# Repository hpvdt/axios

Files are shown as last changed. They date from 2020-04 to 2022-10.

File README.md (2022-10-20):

*This is the repository for our human powered submarine Axios, that we have decided to no longer to pursue. **IT IS NOT COMPLETE, LET ALONE TESTED.***

*Our motivation for making this repository public to to share what progress we did make to help others who might be interested in developing a similar system.*

# Axios

Our attempt at a human powered submarine, titled Axios. Within it there were two electronics systems to be implemented: rebreather monitoring and navigation. These were meant to be operate entirely independently of one another, being powered off separate batteries.

In this repository resides the code and hardware design files prepared for the initial versions of these systems from before the team decided to cancel the project.

Both systems were based around ATmega328P microcontrollers due to the team's familiarity with them and their adaquate amount of peripherals for serving both roles.

## Rebreather System

This was meant to supervise the different gas sensors around the submarine hull to inform the pilot about the atmospheric state within Axios. It collected data from three oxygen sensors and one carbon dioxide (CO2) sensor, it then displayed the value of each on separate seven-segment displays.

Of the two systems prepared for Axios, this was by far the more mature one. It was essentially ready for final deployment.

### Carbon Dioxide Sensing

For monitoring CO2 an MH-Z19 sensor was used which uses infrared to measure CO2 in the air. Getting data with the sensor was simple, it outputs a PWM signal at 1Hz that was trivial to monitor using the ATmega328P. The only hardware needed to interface it with the Arduino was a level shifting transistor to step the 3.3V PWM signal to 5V for the microcontroller to read.

One minor note we were unaware of is that the sensor has a small heater within it which is used to measure the CO2. This means the sensor occasionally draws a surge of current to keep it warm. This caused us to think the system was malfunctioning and drawing excessive power in our preliminary tests.

### Oxygen Sensing

This was the main focus of this board, since we were responsible for reading the raw sensor data. The oxygen sensors we were planning to use were standard oxygen sensors used for SCUBA diving. These are essentially chemical cells that when exposed to varying concentrations of oxygen in the air would vary their voltage proportionally. They had two issues the circuit needed to address:

1. The output voltage was pretty small. About 65mV for a new cell at 100% oxygen, but we would ideally be monitoring 21%, so about 20mV.
2. Although roughly linear, the output at 0% was not 0 mV, but about 15 mV.
3. Being chemical cells, they would gradually degrade and our circuit would need to be tuned for this.

The solution for this was a set of of high precision amplifiers made from operational amplifiers. These would buffer and then amplifier the sensor output to a level more easily read by the ATmega with its internal ADC resolution of about 4 mV. To adjust the circuit for the sensors as they aged we would conduct a two-point calibration (at 100% and 21% oxygen levels) adjusting potentiometers to get the display values to match these conditions.

## Navigation

Axios was designed to be controlled by three servo-actuated control fins. These needed a microcontroller to receive input from the captain (?) and actuate them accordingly. In addition to steering the submarine, it was planned for the captain of Axios to be provided orientation data about the submarine (roll, pitch, yaw), depth information, and power from their pedals. 

This board needs significant revision before it is worthy of installation into any submarine.

### Steering

Steering was to be done using a modified game controller (so we had wires directly to the potentiometers within it) which was read as an analog signal and then following some linear algebra, servo angles would be determined and set. Intentionally a short and simple loop.

There was discussion of a feature to have the submarine maintain depth without user input, but we never reached this stage.

### Orientation Data

Orientation data was meant to be provided by the use of a 9-axis IMU attached to the board. This approach quickly revealed a few key issues:

- The boards were going to move frequently within Axios, and the IMU would need to be calibrated for each new position. This could be remedied by off-boarding the IMU to a set location in Axios.
- The IMU only provided accelerations and magnetic field, we would need to code or find a library to perform the sensor fusion on the ATmega.
   - This would likely lead to significant usage of processor time
   - Our solution may not be able to replicate a more polished sensor even after significant work

Little was done for this as we were planning to transition to another IMU, the BNO055 which would address both of these points.

### Depth Information

Reading the depth was done using a pressure sensor that was connected to a port in the hull. The one we had acquired for Axios output a simple linear output proportional to the pressure sensed and a slight constant offset. Reading this analog signal, then dividing by the specific gravity of water would allow us to accurately estimate our depth in water.

### Pedal Power Data

This was planned to use a Raspberry Pi Zero with an ANT dongle to read available ANT data from the commercial power pedals in Axios and then broadcast it over UART to the microcontroller to display it for the rider.

This never really reached development, although it would likely be heavily based off the working ANT code prepared for [TITAN (2019)](https://github.com/hpvdt/titan_2019).

## Displays

The display system was identical across the boards. Given the amount of pins that needed to be controlled for all the displays a shift register was used for each display to control the segments as the digits were multiplexed by the microcontroller. This meant that all displays on a board could be controller by a handful of pins on the ATmega and a series of daisy-chained shift registers.

Although the two boards would operate separately, they were designed to be roughly arranged as shown below. These displays were meant to be bright enough to pass through the back of the partial mirror used to provide the captain a view.

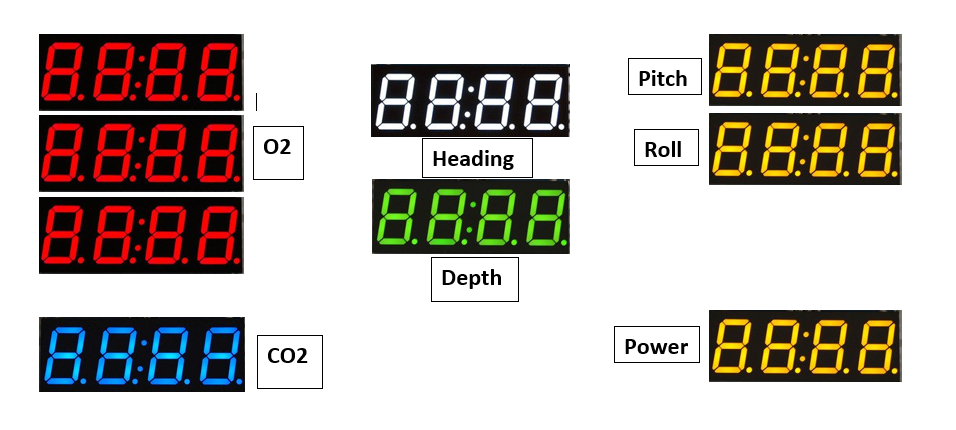
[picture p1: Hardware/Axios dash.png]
Planned Axios layout


# Software Used

For the design of the hardware EAGLE was used. For the microcontroller code it was all prepared using the Arduino IDE.

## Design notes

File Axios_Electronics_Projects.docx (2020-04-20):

# Axios Electronics Projects

Axios is a unique project in many respects, presenting unique challenges and conditions for the electronics to perform in. Reliability and safety are of the utmost importance, and that there is always a ‘fail-safe’ state. All projects are critical unless otherwise noted. All systems need to be splash resistant to a minimum as well.

As with Titan (and probably most of our project going forward,) this system will be powered off several LiFePO4 batteries given their proven stability and safety even when failing.

# Control System

There 3 fins positioned around midway on the sub, spaced 120 degrees apart (front view of the sub to the right). These are positioned using linkages to servos. We need to control these servos based on input from the rider, ideally, they use a single joystick to control pitch, roll, and yaw. This system should be isolated from any other system (excluding navigation).

Tasks for this are:

- Writing code for determining fin angles based on a desired rotation rate
- Getting or making a 3-axis flight stick
  - Must be compact enough to fit in the sub
- Writing code to translate the desired fin angles to servo angles

Skills needed/learned:

- C++ coding
- Basic circuitry
- Potential for circuit board design

# Navigation system

To assist the rider in navigation especially in this unconventional configuration let alone environment, there is a need for navigational sensors. These need to display their data in an easy to read and see location, likely using 7-segment displays for numeric values. This is to me developed alongside the control system and likely share hardware if possible. The data required for the rider are:

- Compass heading, using compass sensor – probably as part of a 9DoF module
- Pitch, using an accelerometer – probably as part of a 9DoF module
- Depth, determined using a special depth sensor

Tasks for this are:

- Writing code for collecting this data
- Writing code for / designing the display circuits

Skills needed/learned:

- C++ coding
- Basic circuitry
- Potential for circuit board design

# Oxygen Sensor System

Absolutely critical! This must be an entirely isolated system of its own. Using three oxygen sensors around the hull, it will display the partial pressure of oxygen in the submarine at each point using 7-segment displays. The values will be to three significant figures between 0 and 1, e.g. 0.201 but it will just display ‘201’.

These sensors output analog signals that will require amplification to be processed by our microcontroller which will require the use of operation amplifiers. The 7-segment display also needs to be prepared but will likely be okay if it is a copy of the ones used for the navigational system.

Skills needed/learned:

- Advanced circuit design
- Micro controller (C/C++) implementation and coding
- Breadboard prototyping
- Circuit board design

# Circuit board design

Pretty self explanatory, design the circuits to connect all the hardware in the sub. Note, there will likely be several different boards present in the sub:

- Control
- Oxygen Sensor
- 7-segment display arrays

Skills needed/learned:

- Circuit design
- Using PCB design software
- Circuit assembly
- Circuit debugging

# Pump System

We need a pump to remove water from our leaks during a ride. This will be a basic system that should only consist of a battery, switch, and pump. All connections should be adequately protected from water.

Pump (has to be high pressure to eject water from the submarine): https://www.banggood.com/FL-3308-130PSI-6LMin-Water-High-Pressure-Diaphragm-Pump-Caravan-Boat-DC12V-p-1071746.html?ID=514178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

Battery: https://hobbyking.com/en_us/zippy-compact-4200mah-4s2p-30c-lifepo4-pack.html?___store=en_us

Skills needed/learned:

- BASIC circuitry
- Basic circuit assembly

# Lights – Optional

In some instances, the sub may need to traverse though darker environments which may need some extra lighting. This is not in the near future however.

Skills needed/learned:

- Circuit design

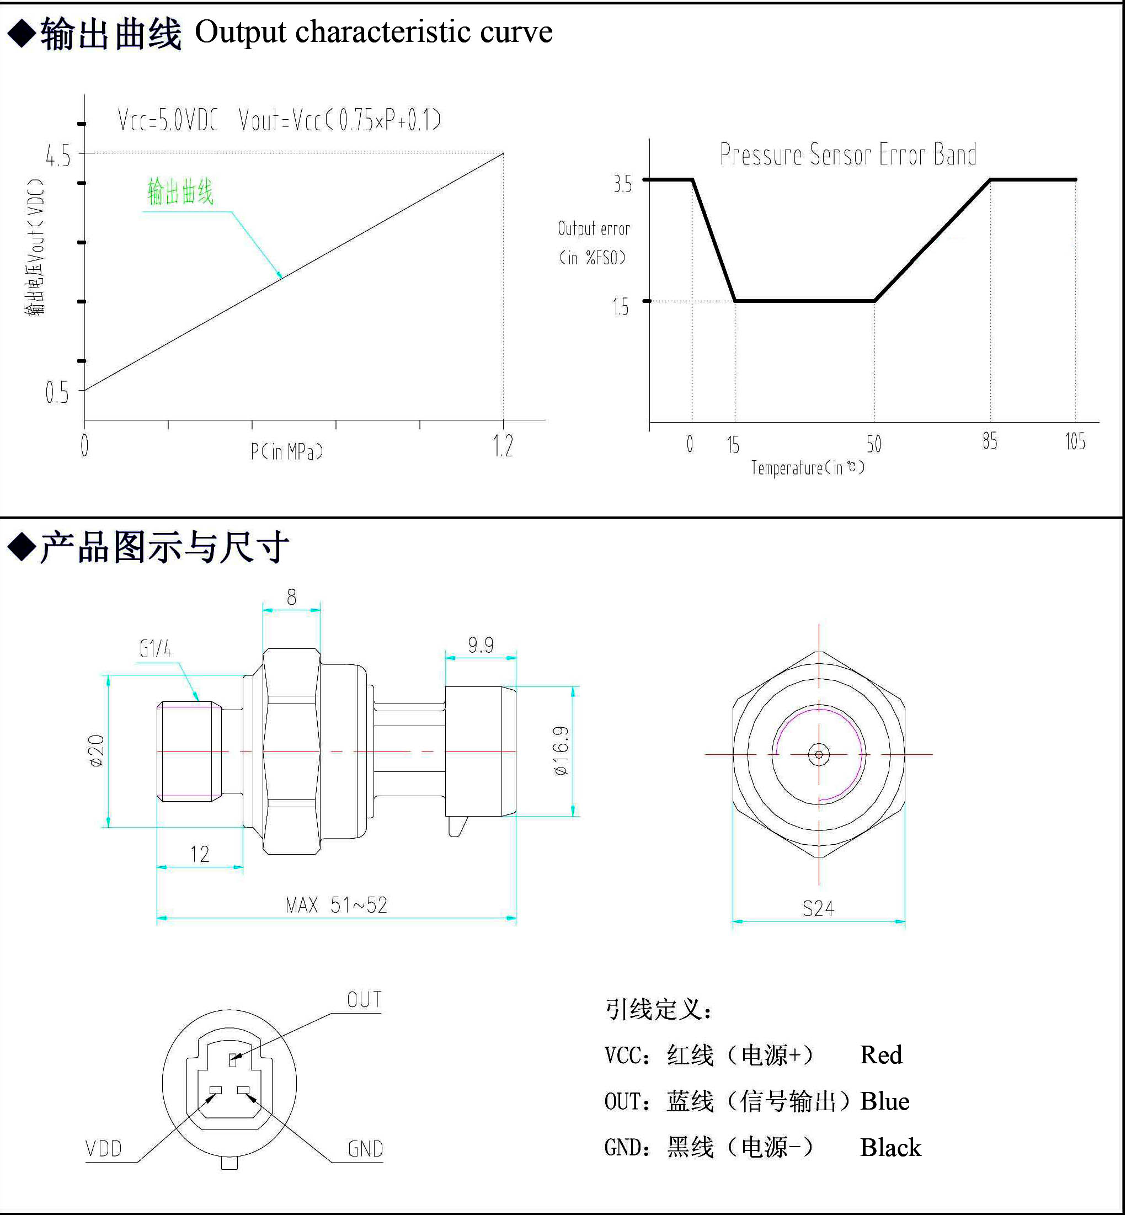
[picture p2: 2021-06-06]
Hardware/control_system/Pressure Sensor Data Sheet.jpg

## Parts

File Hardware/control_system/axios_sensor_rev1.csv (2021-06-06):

Qty | Value | Package | Parts
1 |  | 1X2MTA | J1
7 | 0.1u | C0603 | C2 C4 C6 C8 C10 C12 C18
1 | 0.82u | ECS-MPIL0630-R82MC | L2
1 | 1.5n | C0603 | C5
2 | 1.5u | C0603 | C16 C17
5 | 100k | R0603 | R16 R17 R18 R19 R22
1 | 100u | C0603 | C1
9 | 10k | R0603 | R1 R6 R8 R9 R10 R12 R14 R15 R21
1 | 10n | C0603 | C7
1 | 12k | R0603 | R13
2 | 15k | R0603 | R7 R20
4 | 1k | R0603 | R2 R3 R4 R5
1 | 1u | C0603 | C11
4 | 22u | C0603 | C9 C13 C14 C15
1 | 33u | SRN1060-330M | L1
1 | 47u | C0603 | C3
1 | 52k | R0603 | R11
5 | 7SEGMINI | 7SEGMINI | LED_DEPTH LED_HEADING LED_PITCH LED_POWER LED_ROLL
1 | ACT4065ASH-T | SO8 | U2
1 | AP62600SJ-7 | V-QFN2030-12 | U3
1 | ATMEGA328P_TQFP | TQFP32-08 | U1
5 | CAY16-681J8LF | CAY16-681J8LF | RN1 RN2 RN3 RN4 RN5
1 | CSTNE16M0V530000R0 | CSTCR6M | U$1
1 | CTRL_CONNECT | 1X06 | JP6
1 | Depth Sensor | 1X03 | JP1
1 | ISP | 2X03 | JP7
1 | MPU9250 | MPU9250 | M2
1 | NCP164CSN330T1G | TSOP-5 | U4
1 | SER_CONNECT | 1X06 | JP5
5 | SN74HCS595QPWRQ1 | TSSOP16 | IC2 IC4 IC6 IC8 IC10
1 | Servo1 | 1X03 | JP2
1 | Servo2 | 1X03 | JP3
1 | Servo3 | 1X03 | JP4
1 | V4PAN50-M3 | SMPA | D2
4 | XP231P0201TR | SOT23 | Q1 Q2 Q3 Q4

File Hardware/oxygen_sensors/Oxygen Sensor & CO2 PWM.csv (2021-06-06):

Qty | Value | Device | Package | Parts | Description
3 |  | PINHD-1X2 | 1X02 | SENSOR_1 SENSOR_2 SENSOR_3 | PIN HEADER
32 |  | R-US_R0603 | R0603 | R20 R21 R22 R23 R24 R25 R26 R27 R29 R30 R31 R32 R33 R34 R35 R36 R38 R39 R40 R41 R42 R43 R44 R45 R47 R48 R49 R50 R51 R52 R53 R54 | RESISTOR American symbol
3 | 0.7k | R-US_R0603 | R0603 | R2 R4 R6 | RESISTOR American symbol
7 | 100k | R-US_R0603 | R0603 | R1 R3 R5 R28 R37 R46 R55 | RESISTOR American symbol
2 | 10k | R-US_R0603 | R0603 | R10 R14 | RESISTOR American symbol
6 | 10k | TRIM_US-RJ9W | RJ9W | CAL1 CAL2 CAL3 GAIN_1 GAIN_2 GAIN_3 | POTENTIOMETER
4 | 10n | C-USC0603 | C0603 | C2 C3 C4 C5 | CAPACITOR American symbol
1 | 16MHz | CSTNE16M0V530000R0 | CSTCR6M | Y1
2 | 1u | C-USC0603 | C0603 | C1 C6 | CAPACITOR American symbol
1 | 5V | LD117ASTR | SOT223 | IC3 | Low drop fixed and adjustable positive voltage regulators 1 A
4 | 7SEGMINI | 7SEGMINI | 7SEGMINI | LED2 LED3 LED4 LED5
2 | AD712R | AD712R | SO8 | IC1 IC2 | Dual Precision Low Cost High Speed BiFET Op Amp
1 | ATMEGA328P_TQFP | ATMEGA328P_TQFP | TQFP32-08 | U1 | Popular 328P in QFP
1 | BATT | PINHD-1X2 | 1X02 | BATT | PIN HEADER
1 | CO2 | PINHD-1X3 | 1X03 | CO2 | PIN HEADER
1 | ISP | PINHD-2X3 | 2X03 | ISP | PIN HEADER
1 | SER | PINHD-1X6 | 1X06 | SER | PIN HEADER
4 | SN74HCS595QPWRQ1 | SN74HCS595QPWRQ1 | TSSOP16 | IC4 IC5 IC6 IC7
1 | SST5485 | SST5485 | SOT23 | Q1 | N-Channel JFETs
4 | XP231P0201TR | XP231P0201TR | SOT23 | Q2 Q3 Q4 Q5 | P-Channel Enhancement mode MOSFET

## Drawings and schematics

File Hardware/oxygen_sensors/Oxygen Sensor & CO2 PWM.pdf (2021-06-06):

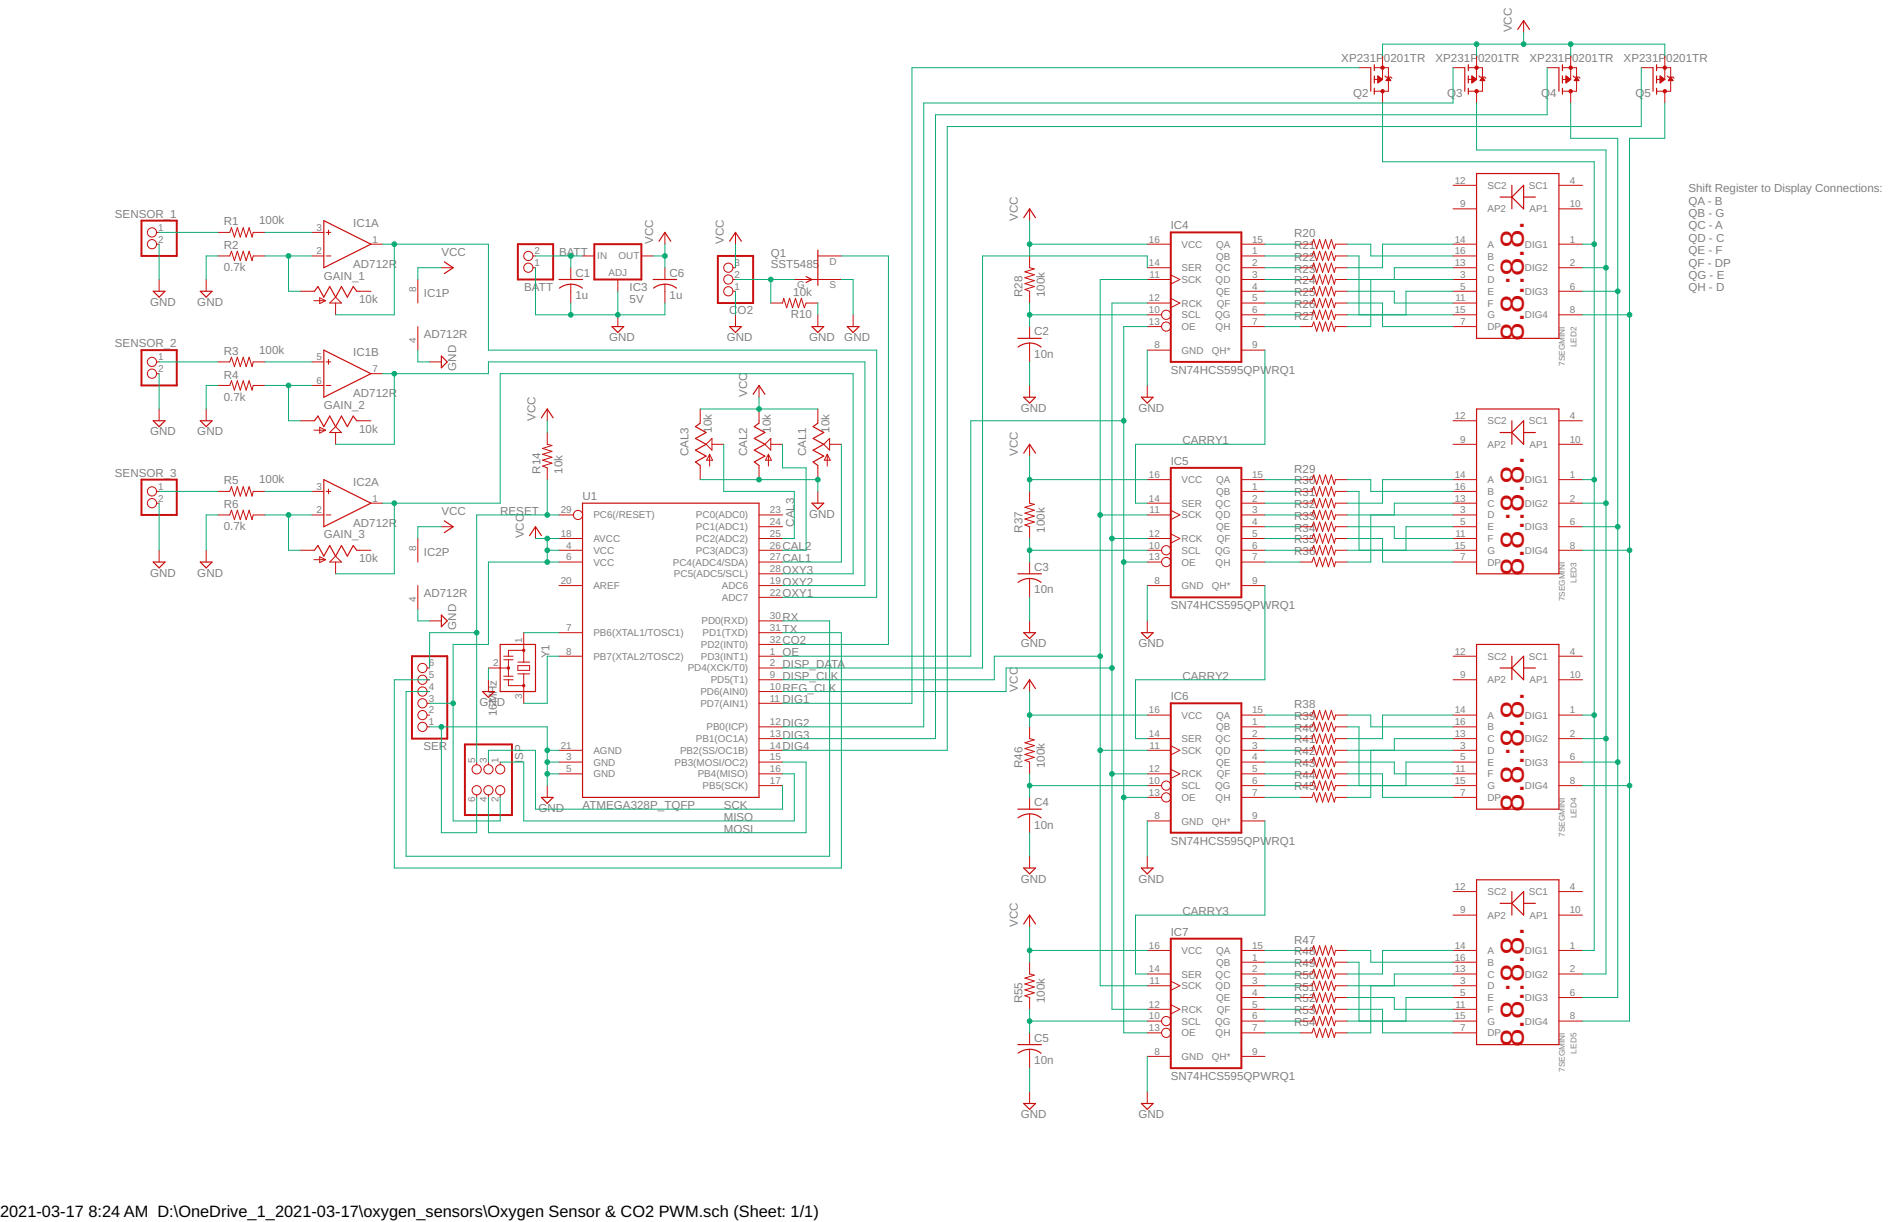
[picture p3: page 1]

Shift Register to Display Connections: QA - B

2 DIG3

6 DIG4 8

2021-03-17 8:24 AM D:\OneDrive_1_2021-03-17\oxygen_sensors\Oxygen Sensor & CO2 PWM.sch (Sheet: 1/1)

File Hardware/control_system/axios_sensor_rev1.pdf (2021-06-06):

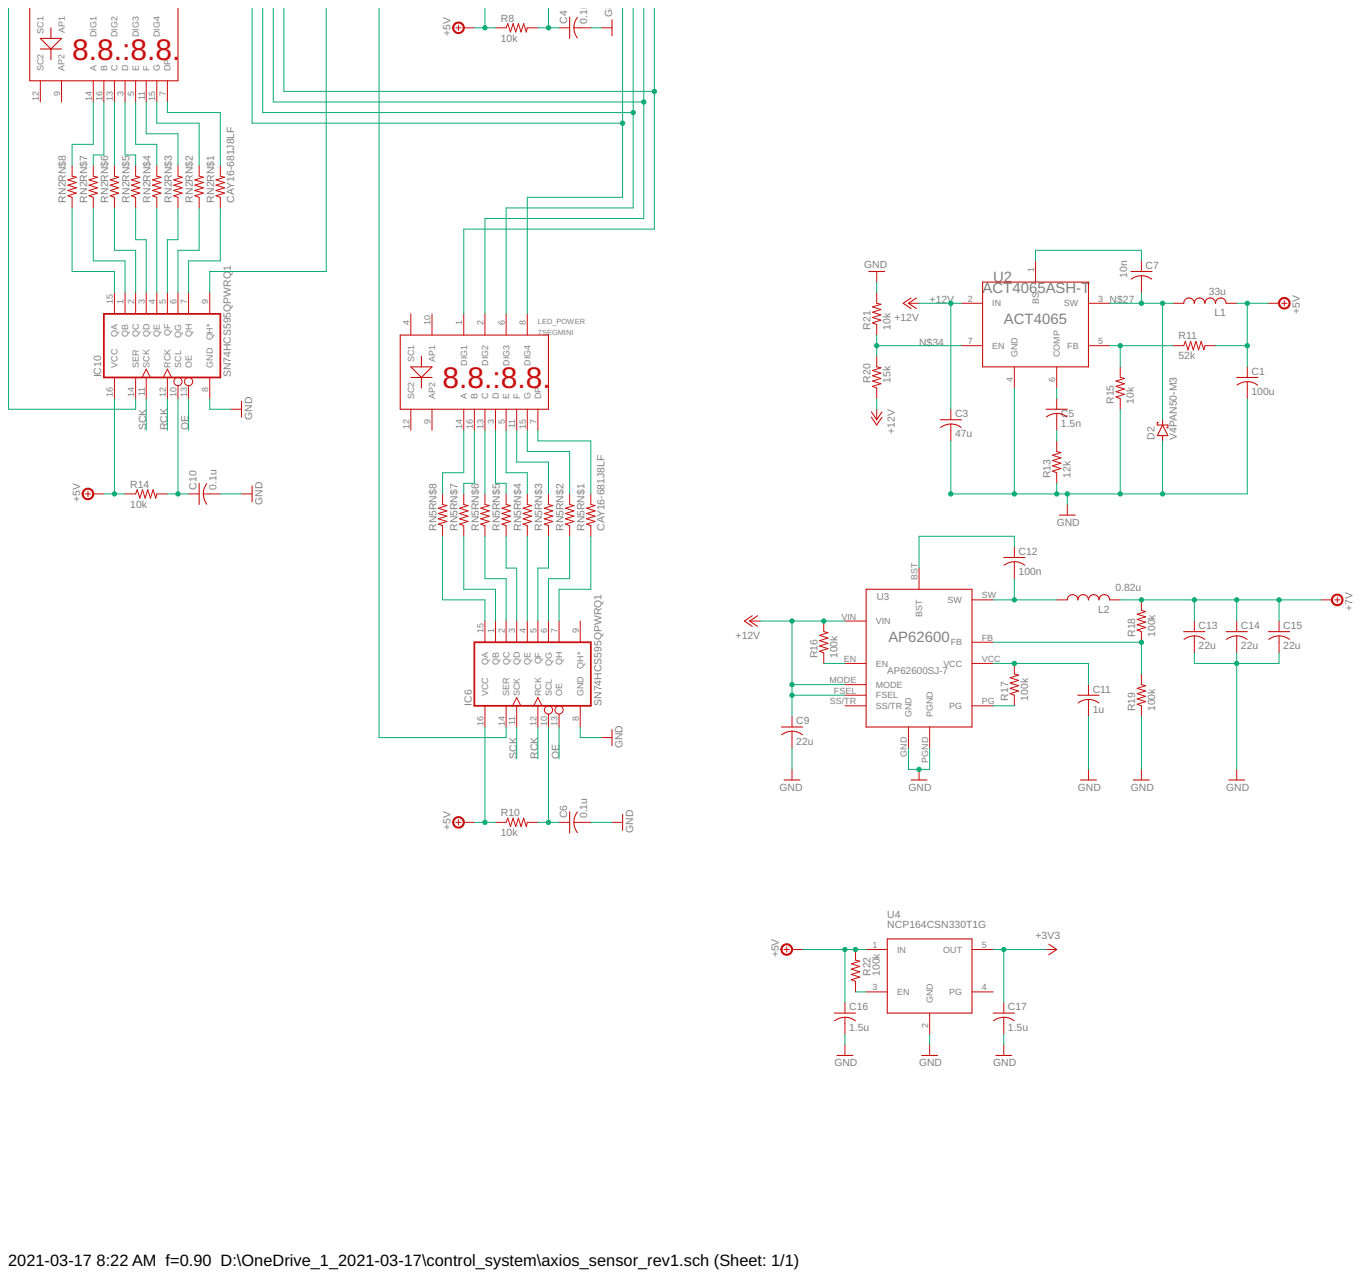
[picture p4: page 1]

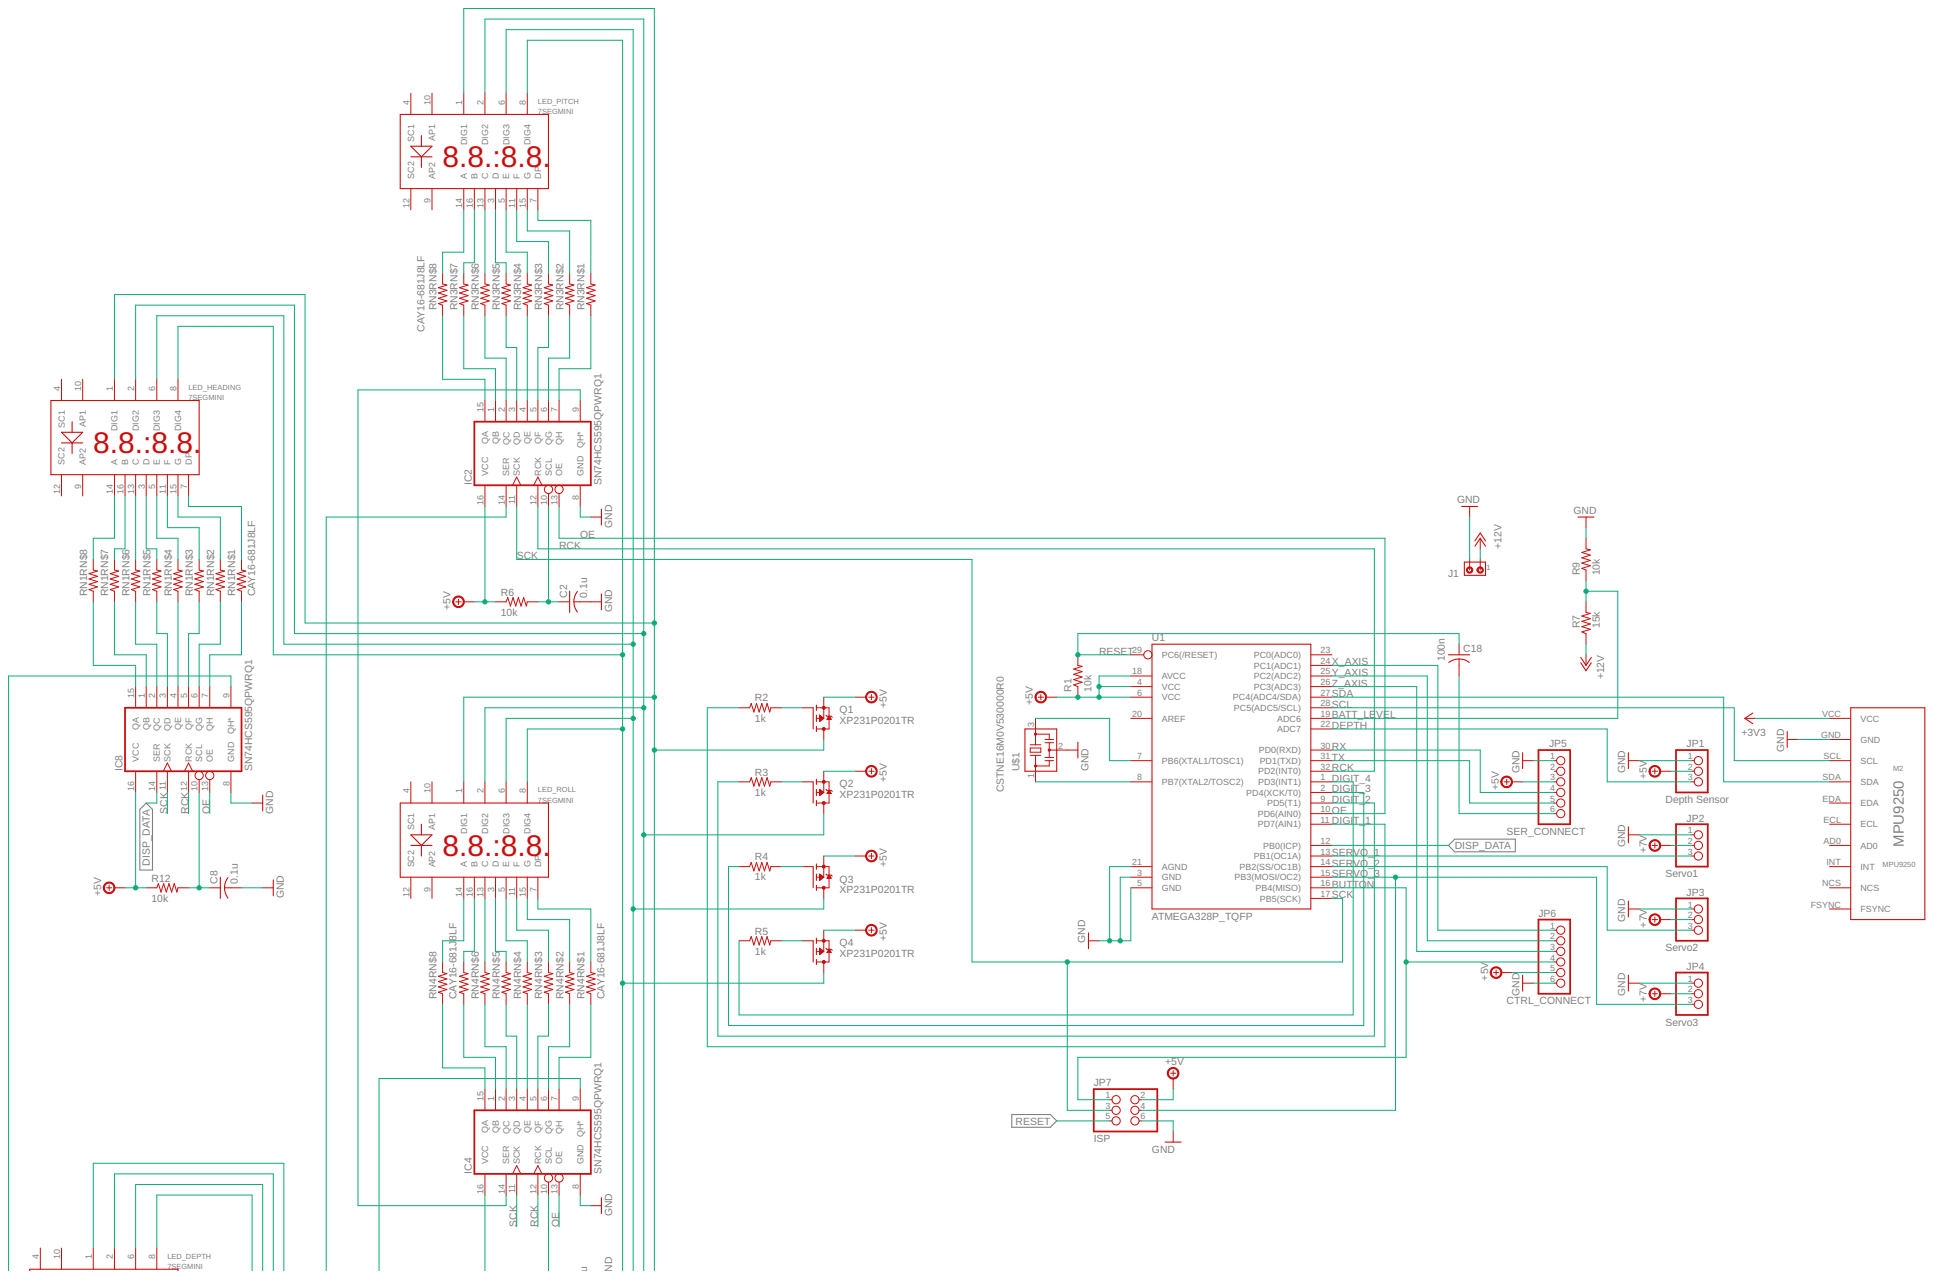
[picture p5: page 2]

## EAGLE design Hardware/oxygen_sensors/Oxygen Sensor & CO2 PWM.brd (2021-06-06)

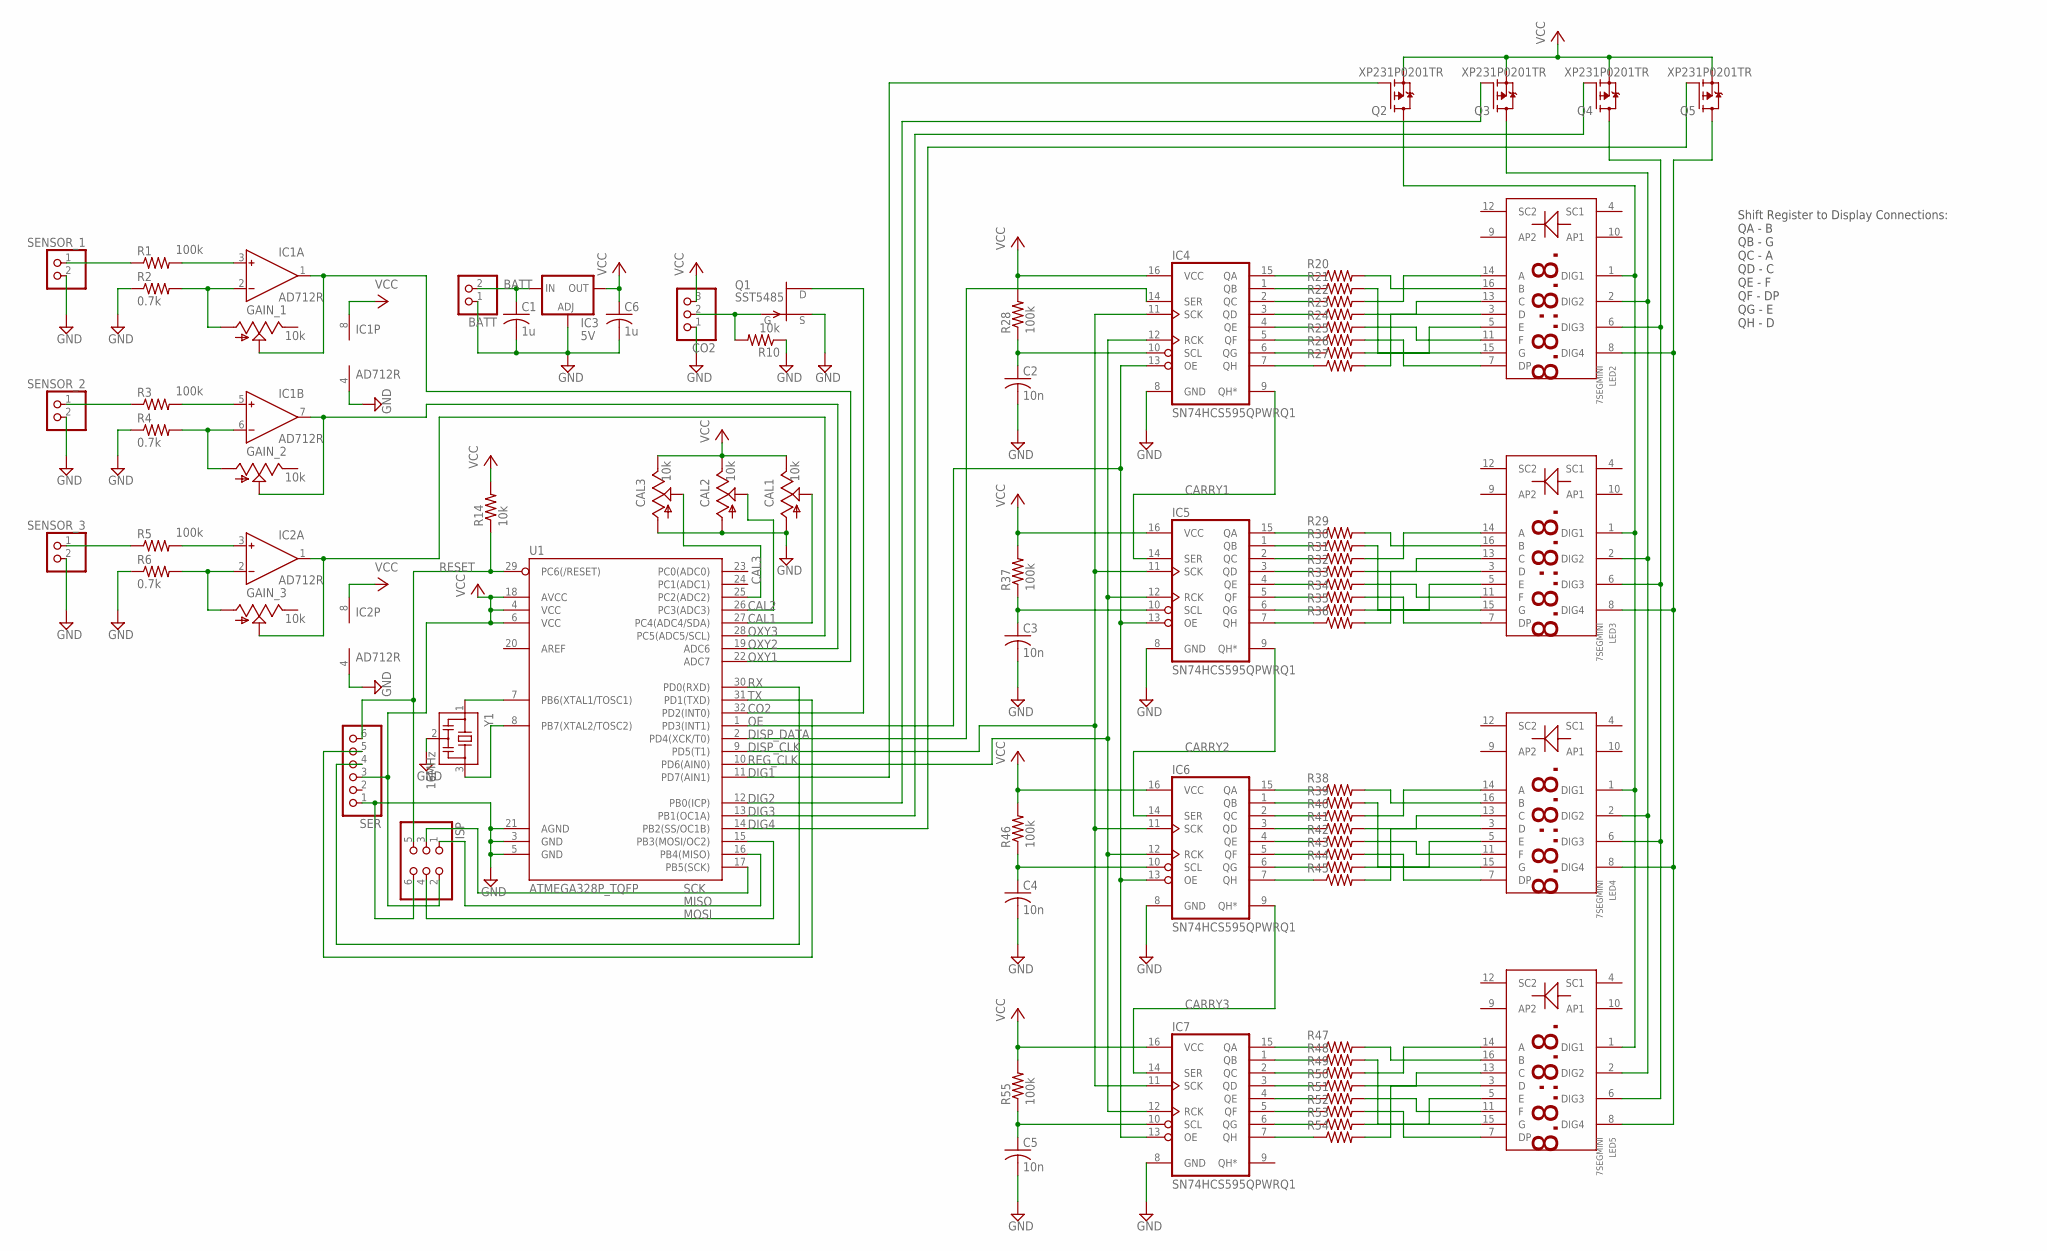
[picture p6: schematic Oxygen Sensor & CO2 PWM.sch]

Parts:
BATT: BATT; 1X02
C1, C6: 1u; C0603
C2, C3, C4, C5: 10n; C0603
CAL1, CAL2, CAL3: 10k; RJ9W
CO2: CO2; 1X03
GAIN_1, GAIN_2, GAIN_3: 10k; RJ9W
IC1, IC2: AD712R; SO8
IC3: 5V; SOT223
IC4, IC5, IC6, IC7: SN74HCS595QPWRQ1; TSSOP16
ISP: ISP; 2X03
LED2, LED3, LED4, LED5: 7SEGMINI
Q1: SST5485; SOT23
Q2, Q3, Q4, Q5: XP231P0201TR; SOT23
R1, R3, R5, R28, R37, R46, R55: 100k; R0603
R2, R4, R6: 0.7k; R0603
R10, R14: 10k; R0603
R20, R21, R22, R23, R24, R25, R26, R27, R29, R30, R31, R32, R33, R34, R35, R36, R38, R39, R40, R41, R42, R43, R44, R45, R47, R48, R49, R50, R51, R52, R53, R54: R-US_R0603; R0603
SENSOR_1, SENSOR_2, SENSOR_3: PINHD-1X2; 1X02
SER: SER; 1X06
U1: ATMEGA328P_TQFP; TQFP32-08
Y1: 16MHz; CSTCR6M

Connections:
BATT: BATT.2, C1.1, IC3.3 (IN)
CAL1: CAL1.S, U1.27 (PC4(ADC4/SDA))
CAL2: CAL2.S, U1.26 (PC3(ADC3))
CAL3: CAL3.S, U1.25 (PC2(ADC2))
CARRY1: IC4.9 (QH*), IC5.14 (SER)
CARRY2: IC5.9 (QH*), IC6.14 (SER)
CARRY3: IC6.9 (QH*), IC7.14 (SER)
CO2: Q1.1 (D), U1.32 (PD2(INT0))
CO2_PWM: CO2.2, Q1.3 (G), R10.2
COM_D1: LED2.1 (DIG1), LED3.1 (DIG1), LED4.1 (DIG1), LED5.1 (DIG1), Q2.3 (D)
COM_D2: LED2.2 (DIG2), LED3.2 (DIG2), LED4.2 (DIG2), LED5.2 (DIG2), Q3.3 (D)
COM_D3: LED2.6 (DIG3), LED3.6 (DIG3), LED4.6 (DIG3), LED5.6 (DIG3), Q4.3 (D)
COM_D4: LED2.8 (DIG4), LED3.8 (DIG4), LED4.8 (DIG4), LED5.8 (DIG4), Q5.3 (D)
DIG1: Q2.1 (G), U1.11 (PD7(AIN1))
DIG2: Q3.1 (G), U1.12 (PB0(ICP))
DIG3: Q4.1 (G), U1.13 (PB1(OC1A))
DIG4: Q5.1 (G), U1.14 (PB2(SS/OC1B))
DISP_CLK: IC4.11 (SCK), IC5.11 (SCK), IC6.11 (SCK), IC7.11 (SCK), U1.9 (PD5(T1))
DISP_DATA: IC4.14 (SER), U1.2 (PD4(XCK/T0))
GND: BATT.1, C1.2, C2.2, C3.2, C4.2, C5.2, C6.2, CAL1.A, CAL2.A, CAL3.A, CO2.1, IC1.4 (V-), IC2.4 (V-), IC3.1 (ADJ), IC4.8 (GND), IC5.8 (GND), IC6.8 (GND), IC7.8 (GND), ISP.6, Q1.2 (S), R2.1, R4.1, R6.1, R10.1, SENSOR_1.2, SENSOR_2.2, SENSOR_3.2, SER.1, U1.3 (GND), U1.5 (GND), U1.21 (AGND), Y1.2
MISO: ISP.1, U1.16 (PB4(MISO))
MOSI: ISP.4, U1.15 (PB3(MOSI/OC2))
unnamed: IC1.3 (IN+), R1.2
unnamed: GAIN_1.A, IC1.2 (IN-), R2.2
unnamed: IC1.5 (IN+), R3.2
unnamed: GAIN_2.A, IC1.6 (IN-), R4.2
unnamed: IC2.3 (IN+), R5.2
unnamed: GAIN_3.A, IC2.2 (IN-), R6.2
unnamed: U1.7 (PB6(XTAL1/TOSC1)), Y1.1
unnamed: U1.8 (PB7(XTAL2/TOSC2)), Y1.3
unnamed: IC4.15 (QA), R20.1
unnamed: IC4.1 (QB), R21.1
unnamed: IC4.2 (QC), R22.1
unnamed: IC4.3 (QD), R23.1
unnamed: IC4.4 (QE), R24.1
unnamed: IC4.5 (QF), R25.1
unnamed: IC4.6 (QG), R26.1
unnamed: IC4.7 (QH), R27.1
unnamed: C2.1, IC4.10 (SCL), R28.1
unnamed: LED2.16 (B), R20.2
unnamed: LED2.15 (G), R21.2
unnamed: LED2.14 (A), R22.2
unnamed: LED2.13 (C), R23.2
unnamed: LED2.11 (F), R24.2
unnamed: LED2.7 (DP), R25.2
unnamed: LED2.5 (E), R26.2
unnamed: LED2.3 (D), R27.2
unnamed: IC5.15 (QA), R29.1
unnamed: IC5.1 (QB), R30.1
unnamed: IC5.2 (QC), R31.1
unnamed: IC5.3 (QD), R32.1
unnamed: IC5.4 (QE), R33.1
unnamed: IC5.5 (QF), R34.1
unnamed: IC5.6 (QG), R35.1
unnamed: IC5.7 (QH), R36.1
unnamed: C3.1, IC5.10 (SCL), R37.1
unnamed: LED3.16 (B), R29.2
unnamed: LED3.15 (G), R30.2
unnamed: LED3.14 (A), R31.2
unnamed: LED3.13 (C), R32.2
unnamed: LED3.11 (F), R33.2
unnamed: LED3.7 (DP), R34.2
unnamed: LED3.5 (E), R35.2
unnamed: LED3.3 (D), R36.2
unnamed: IC6.15 (QA), R38.1
unnamed: IC6.1 (QB), R39.1
unnamed: IC6.2 (QC), R40.1
unnamed: IC6.3 (QD), R41.1
unnamed: IC6.4 (QE), R42.1
unnamed: IC6.5 (QF), R43.1
unnamed: IC6.6 (QG), R44.1
unnamed: IC6.7 (QH), R45.1
unnamed: C4.1, IC6.10 (SCL), R46.1
unnamed: LED4.16 (B), R38.2
unnamed: LED4.15 (G), R39.2
unnamed: LED4.14 (A), R40.2
unnamed: LED4.13 (C), R41.2
unnamed: LED4.11 (F), R42.2
unnamed: LED4.7 (DP), R43.2
unnamed: LED4.5 (E), R44.2
unnamed: LED4.3 (D), R45.2
unnamed: IC7.15 (QA), R47.1
unnamed: IC7.1 (QB), R48.1
unnamed: IC7.2 (QC), R49.1
unnamed: IC7.3 (QD), R50.1
unnamed: IC7.4 (QE), R51.1
unnamed: IC7.5 (QF), R52.1
unnamed: IC7.6 (QG), R53.1
unnamed: IC7.7 (QH), R54.1
unnamed: C5.1, IC7.10 (SCL), R55.1
unnamed: LED5.16 (B), R47.2
unnamed: LED5.15 (G), R48.2
unnamed: LED5.14 (A), R49.2
unnamed: LED5.13 (C), R50.2
unnamed: LED5.11 (F), R51.2
unnamed: LED5.7 (DP), R52.2
unnamed: LED5.5 (E), R53.2
unnamed: LED5.3 (D), R54.2
O2SENS_1: R1.1, SENSOR_1.1
O2SENS_2: R3.1, SENSOR_2.1
O2SENS_3: R5.1, SENSOR_3.1
OE: IC4.13 (OE), IC5.13 (OE), IC6.13 (OE), IC7.13 (OE), U1.1 (PD3(INT1))
OXY1: GAIN_1.S, IC1.1 (OUT), U1.22 (ADC7)
OXY2: GAIN_2.S, IC1.7 (OUT), U1.19 (ADC6)
OXY3: GAIN_3.S, IC2.1 (OUT), U1.28 (PC5(ADC5/SCL))
REG_CLK: IC4.12 (RCK), IC5.12 (RCK), IC6.12 (RCK), IC7.12 (RCK), U1.10 (PD6(AIN0))
RESET: ISP.5, R14.1, SER.6, U1.29 (PC6(/RESET))
RX: SER.4, U1.30 (PD0(RXD))
SCK: ISP.3, U1.17 (PB5(SCK))
TX: SER.5, U1.31 (PD1(TXD))
VCC: C6.1, CAL1.E, CAL2.E, CAL3.E, CO2.3, IC1.8 (V+), IC2.8 (V+), IC3.4 (OUT), IC4.16 (VCC), IC5.16 (VCC), IC6.16 (VCC), IC7.16 (VCC), ISP.2, Q2.2 (S), Q3.2 (S), Q4.2 (S), Q5.2 (S), R14.2, R28.2, R37.2, R46.2, R55.2, SER.3, U1.4 (VCC), U1.6 (VCC), U1.18 (AVCC)

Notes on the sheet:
Shift Register to Display Connections: QA - B QB - G QC - A QD - C QE - F QF - DP QG - E QH - D

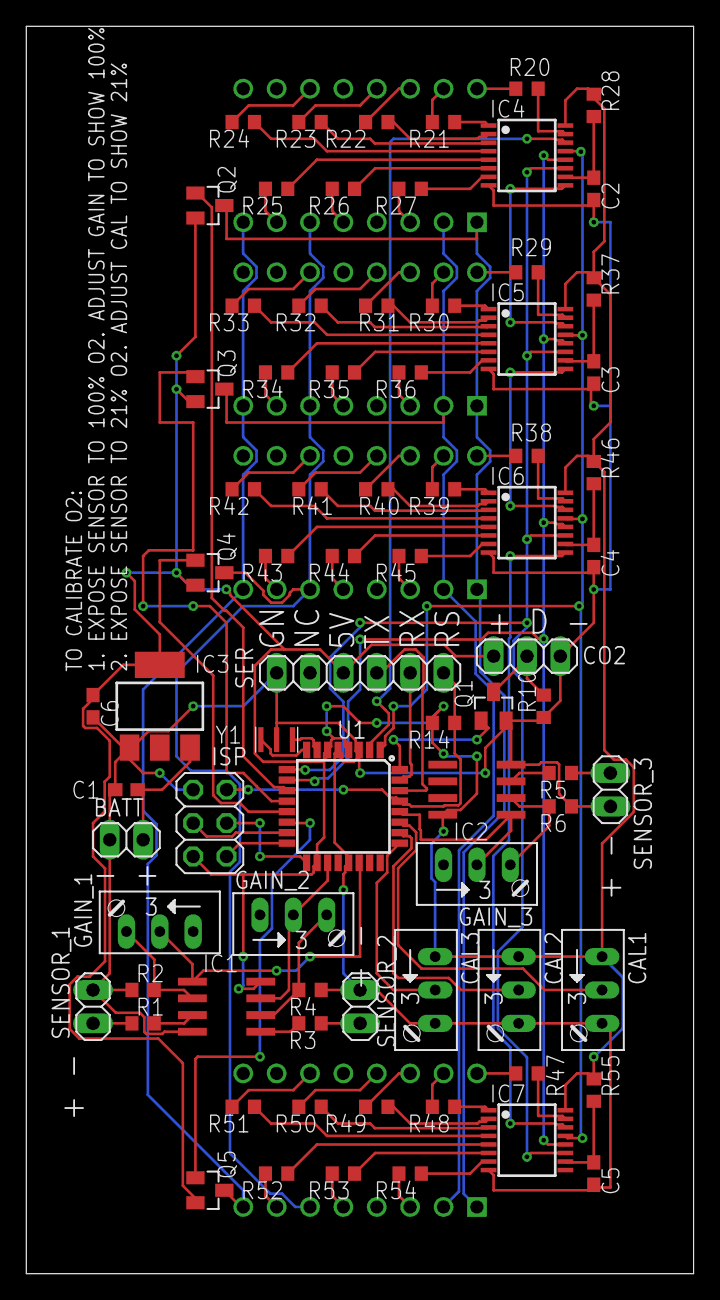
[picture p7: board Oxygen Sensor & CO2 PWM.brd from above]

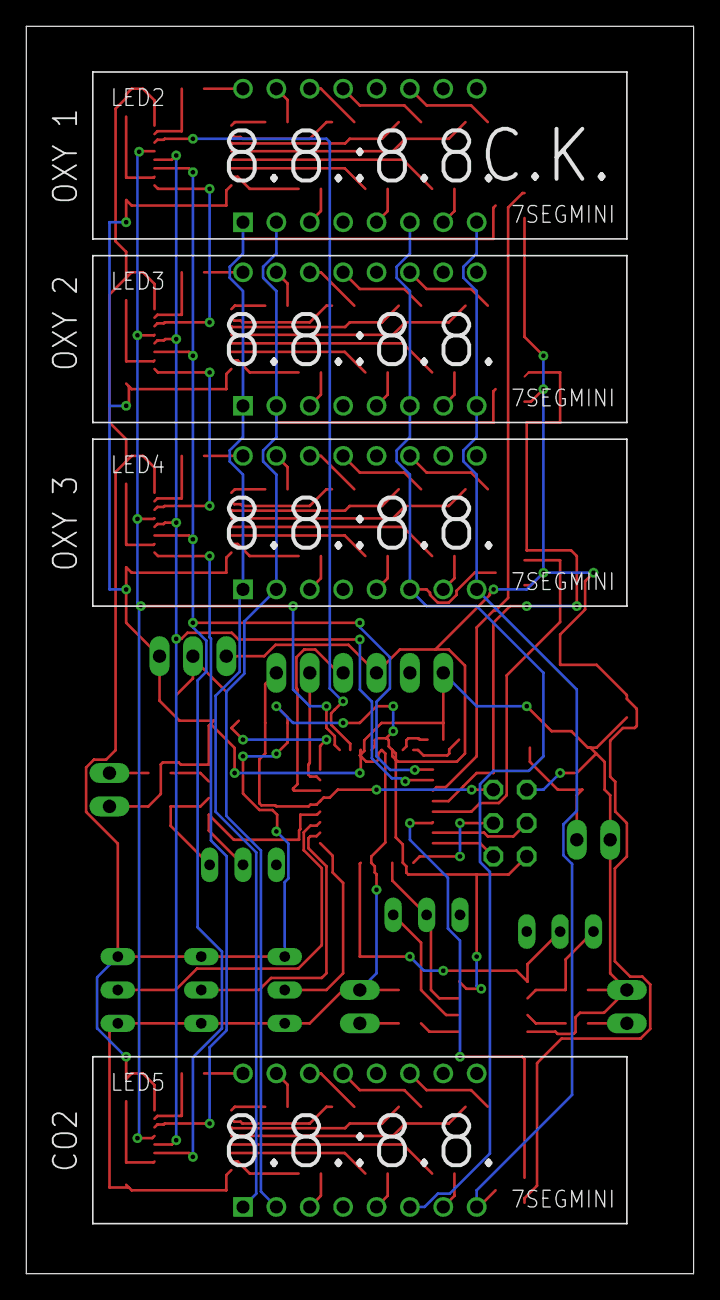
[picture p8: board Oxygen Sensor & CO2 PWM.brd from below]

Board: 2 copper layers, 50.8 x 94.9 mm, 81 parts (4 on the bottom side), 111 nets.

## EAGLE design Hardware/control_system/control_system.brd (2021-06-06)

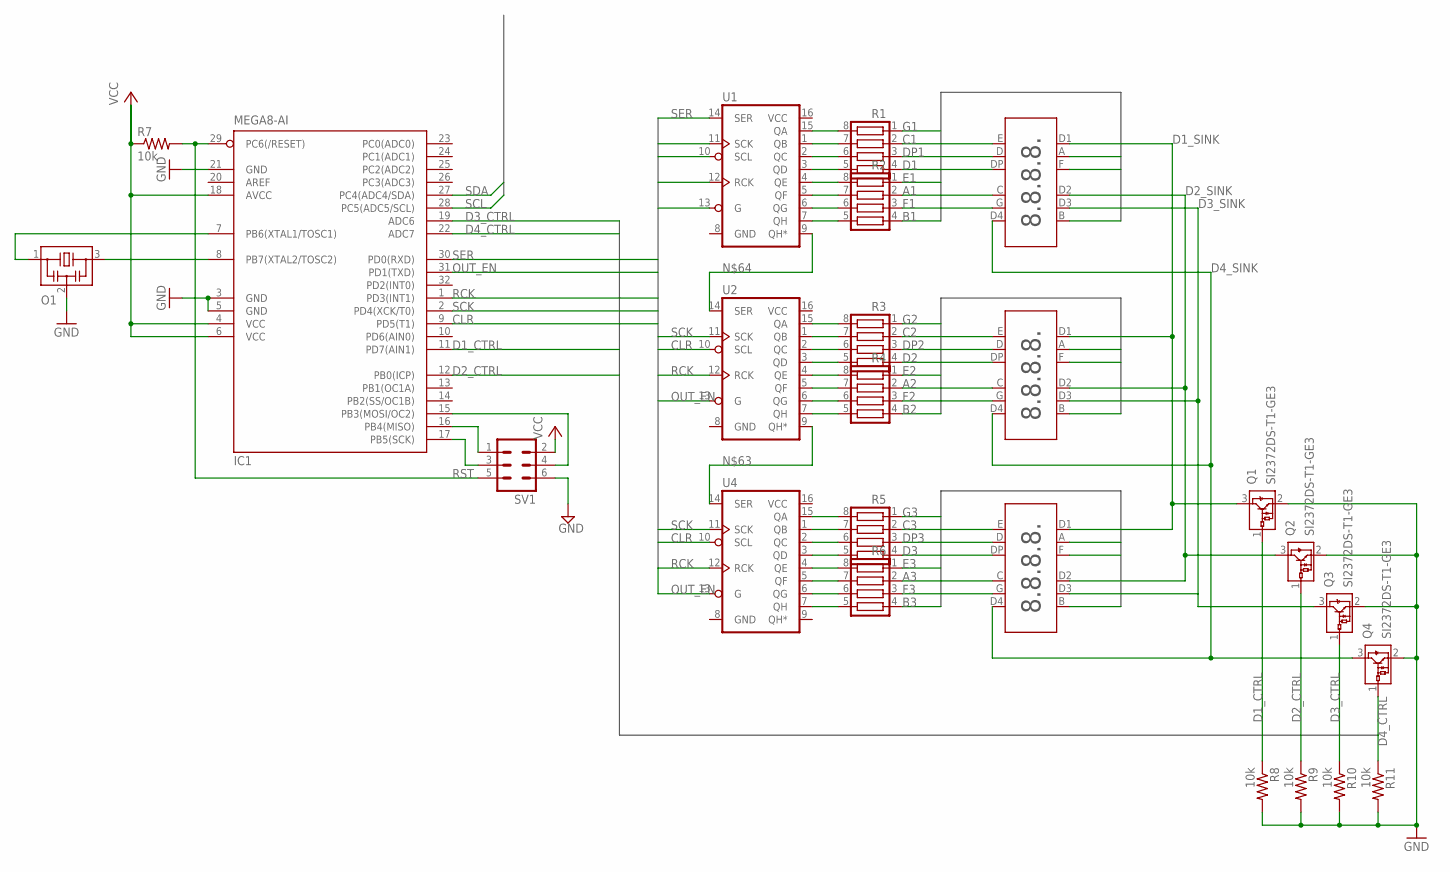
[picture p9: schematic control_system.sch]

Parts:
IC1: MEGA8-AI; TQFP32-08
LED1, LED2, LED3: 7SEG20MM
O1: CSTNE16M0V530000R0; CSTCR6M
Q1, Q2, Q3, Q4: SI2372DS-T1-GE3; SOT23
R1, R2, R3, R4, R5, R6: 220; RESCAXS50P200X150X50-8N
R7, R8, R9, R10, R11: 10k; R0402
SV1: MA03-2
U1, U2, U4: 74595; TSSOP16

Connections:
A1: LED1.A, R2.2
A2: LED2.A, R4.2
A3: LED3.A, R6.2
B1: LED1.B, R2.4
B2: LED2.B, R4.4
B3: LED3.B, R6.4
C1: LED1.C, R1.2
C2: LED2.C, R3.2
C3: LED3.C, R5.2
CLR: IC1.9 (PD5(T1)), U1.10 (SCL), U2.10 (SCL), U4.10 (SCL)
D1: LED1.D, R1.4
D1_CTRL: IC1.11 (PD7(AIN1)), Q1.1 (VIN), R8.1
D1_SINK: LED1.D1, LED2.D1, LED3.D1, Q1.3 (VOUT)
D2: LED2.D, R3.4
D2_CTRL: IC1.12 (PB0(ICP)), Q2.1 (VIN), R9.1
D2_SINK: LED1.D2, LED2.D2, LED3.D2, Q2.3 (VOUT)
D3: LED3.D, R5.4
D3_CTRL: IC1.19 (ADC6), Q3.1 (VIN), R10.1
D3_SINK: LED1.D3, LED2.D3, LED3.D3, Q3.3 (VOUT)
D4_CTRL: IC1.22 (ADC7), Q4.1 (VIN), R11.1
D4_SINK: LED1.D4, LED2.D4, LED3.D4, Q4.3 (VOUT)
DP1: LED1.DP, R1.3
DP2: LED2.DP, R3.3
DP3: LED3.DP, R5.3
E1: LED1.E, R2.1
E2: LED2.E, R4.1
E3: LED3.E, R6.1
F1: LED1.F, R2.3
F2: LED2.F, R4.3
F3: LED3.F, R6.3
G1: LED1.G, R1.1
G2: LED2.G, R3.1
G3: LED3.G, R5.1
GND: IC1.3 (GND), IC1.5 (GND), IC1.21 (GND), O1.2, Q1.2 (GND), Q2.2 (GND), Q3.2 (GND), Q4.2 (GND), R8.2, R9.2, R10.2, R11.2, SV1.6, U1.8 (GND), U2.8 (GND), U4.8 (GND)
MISO: IC1.16 (PB4(MISO)), SV1.1
MOSI: IC1.15 (PB3(MOSI/OC2)), SV1.4
unnamed: R1.8, U1.15 (QA)
unnamed: R1.7, U1.1 (QB)
unnamed: R1.6, U1.2 (QC)
unnamed: R1.5, U1.3 (QD)
unnamed: R2.8, U1.4 (QE)
unnamed: R2.7, U1.5 (QF)
unnamed: R2.6, U1.6 (QG)
unnamed: R2.5, U1.7 (QH)
unnamed: IC1.7 (PB6(XTAL1/TOSC1)), O1.1
unnamed: IC1.8 (PB7(XTAL2/TOSC2)), O1.3
unnamed: R3.8, U2.15 (QA)
unnamed: R3.7, U2.1 (QB)
unnamed: R3.6, U2.2 (QC)
unnamed: R3.5, U2.3 (QD)
unnamed: R4.8, U2.4 (QE)
unnamed: R4.7, U2.5 (QF)
unnamed: R4.6, U2.6 (QG)
unnamed: R4.5, U2.7 (QH)
unnamed: R5.8, U4.15 (QA)
unnamed: R5.7, U4.1 (QB)
unnamed: R5.6, U4.2 (QC)
unnamed: R5.5, U4.3 (QD)
unnamed: R6.8, U4.4 (QE)
unnamed: R6.7, U4.5 (QF)
unnamed: R6.6, U4.6 (QG)
unnamed: R6.5, U4.7 (QH)
unnamed: U2.9 (QH*), U4.14 (SER)
unnamed: U1.9 (QH*), U2.14 (SER)
OUT_EN: IC1.31 (PD1(TXD)), U1.13 (G), U2.13 (G), U4.13 (G)
RCK: IC1.1 (PD3(INT1)), U1.12 (RCK), U2.12 (RCK), U4.12 (RCK)
RST: IC1.29 (PC6(/RESET)), R7.2, SV1.5
SCK: IC1.2 (PD4(XCK/T0)), U1.11 (SCK), U2.11 (SCK), U4.11 (SCK)
SCK1: IC1.17 (PB5(SCK)), SV1.3
SCL: IC1.28 (PC5(ADC5/SCL))
SDA: IC1.27 (PC4(ADC4/SDA))
SER: IC1.30 (PD0(RXD)), U1.14 (SER)
VCC: IC1.4 (VCC), IC1.6 (VCC), IC1.18 (AVCC), R7.1, SV1.2, U1.16 (VCC), U2.16 (VCC), U4.16 (VCC)

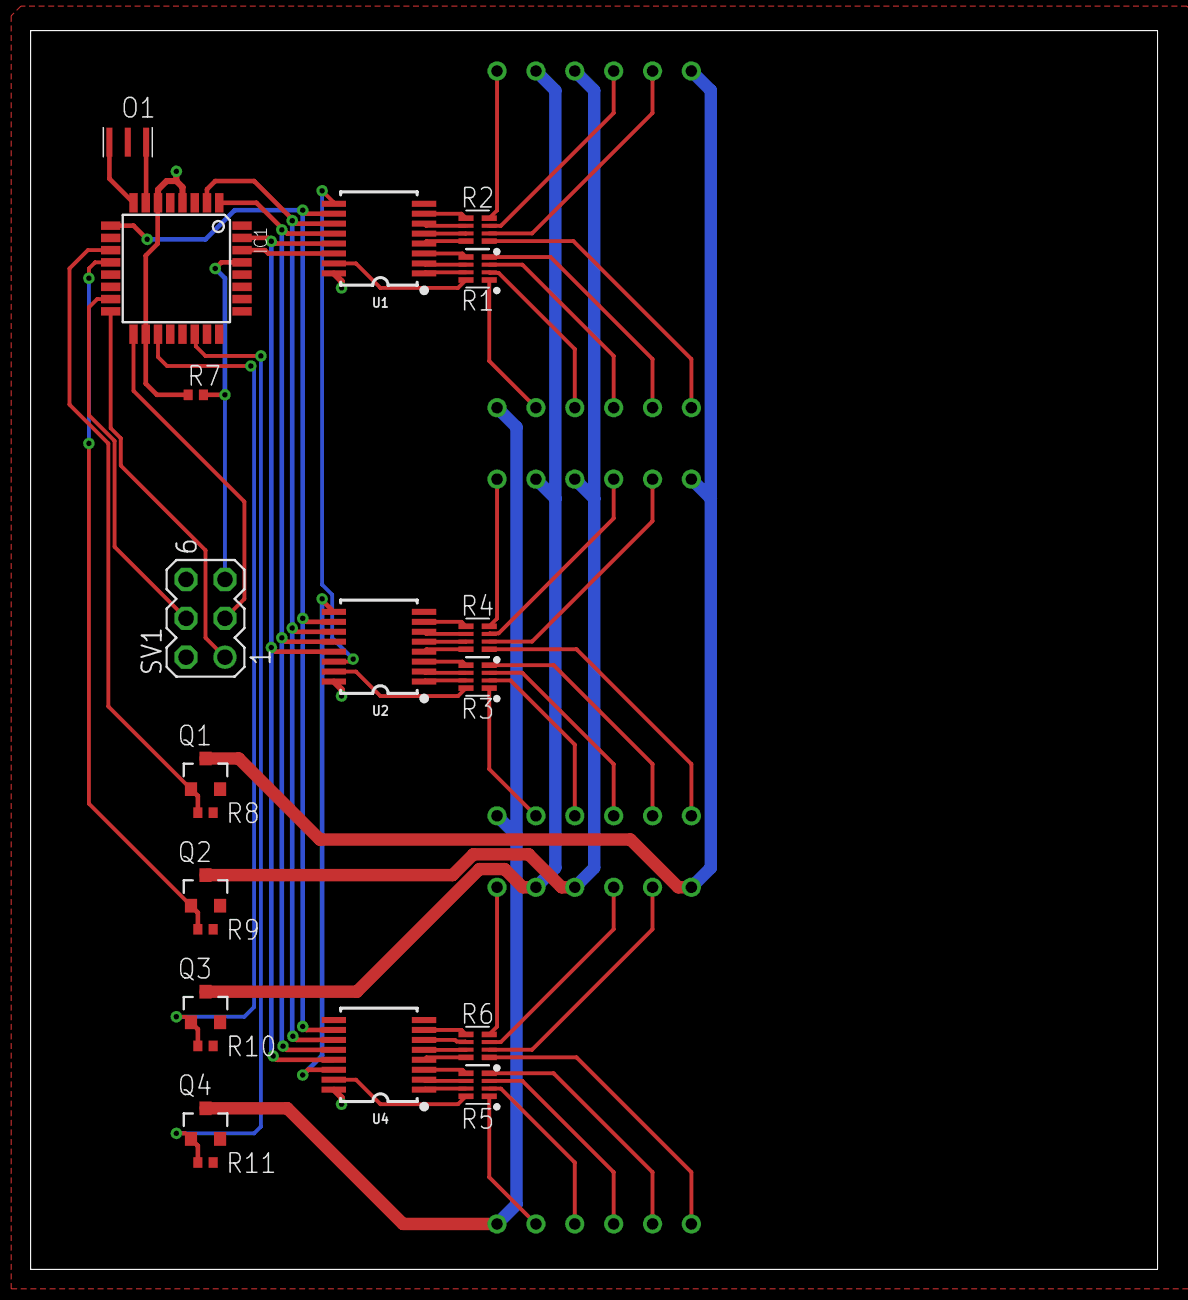
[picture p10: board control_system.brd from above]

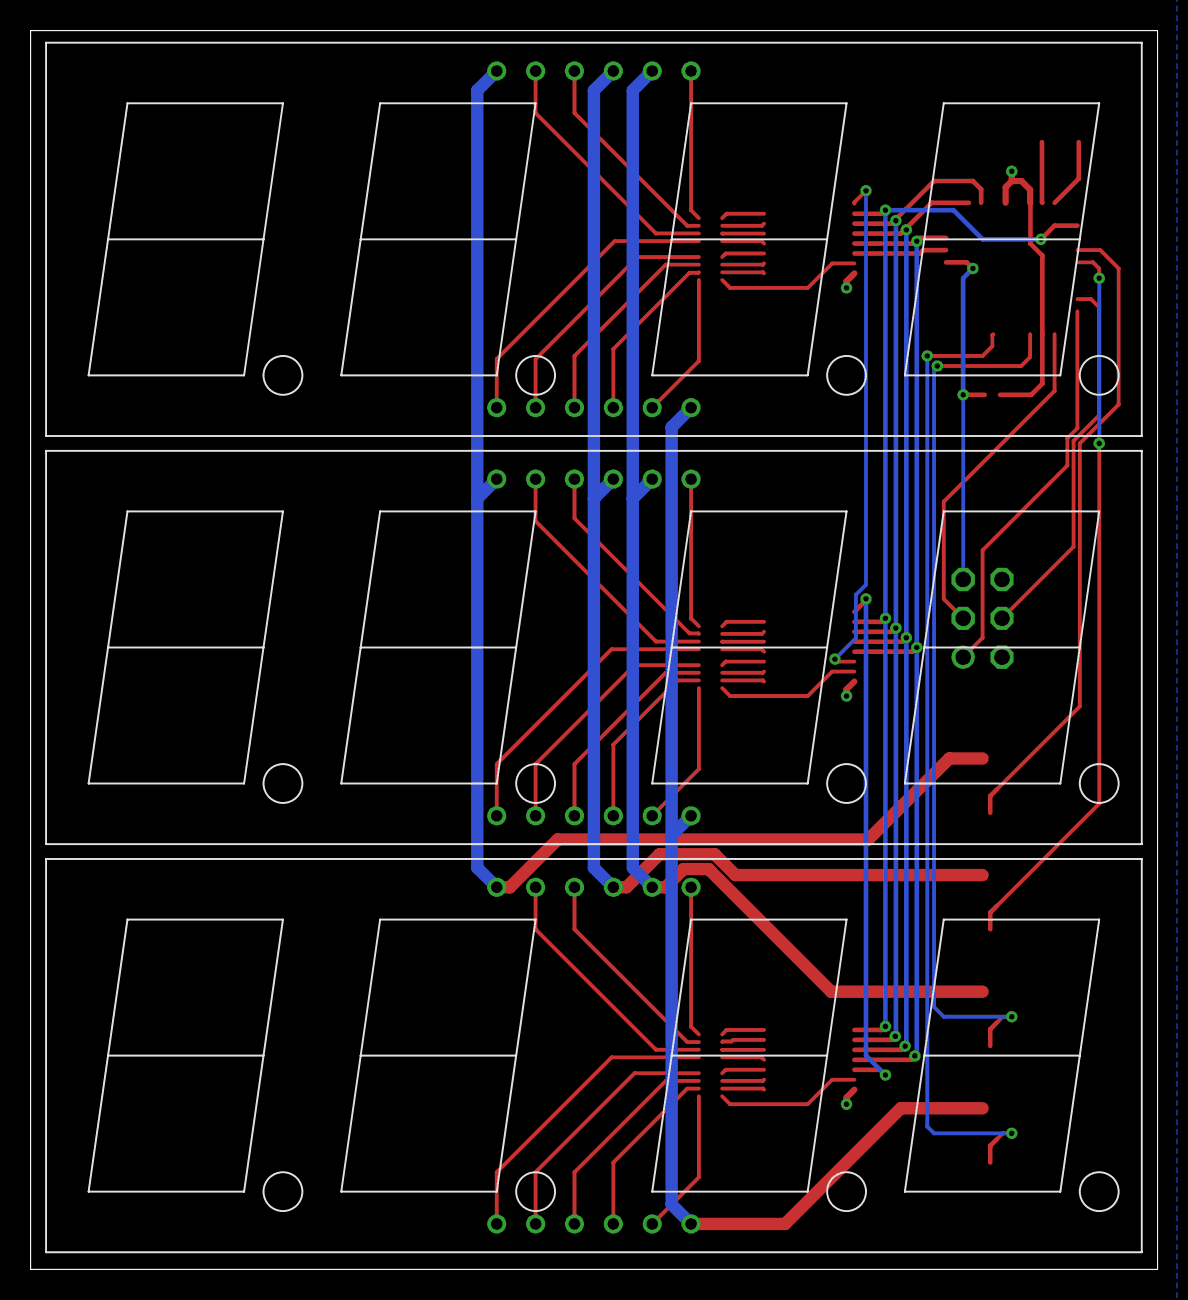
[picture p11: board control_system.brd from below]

Board: 2 copper layers, 73.6 x 81.0 mm, 24 parts (3 on the bottom side), 71 nets.

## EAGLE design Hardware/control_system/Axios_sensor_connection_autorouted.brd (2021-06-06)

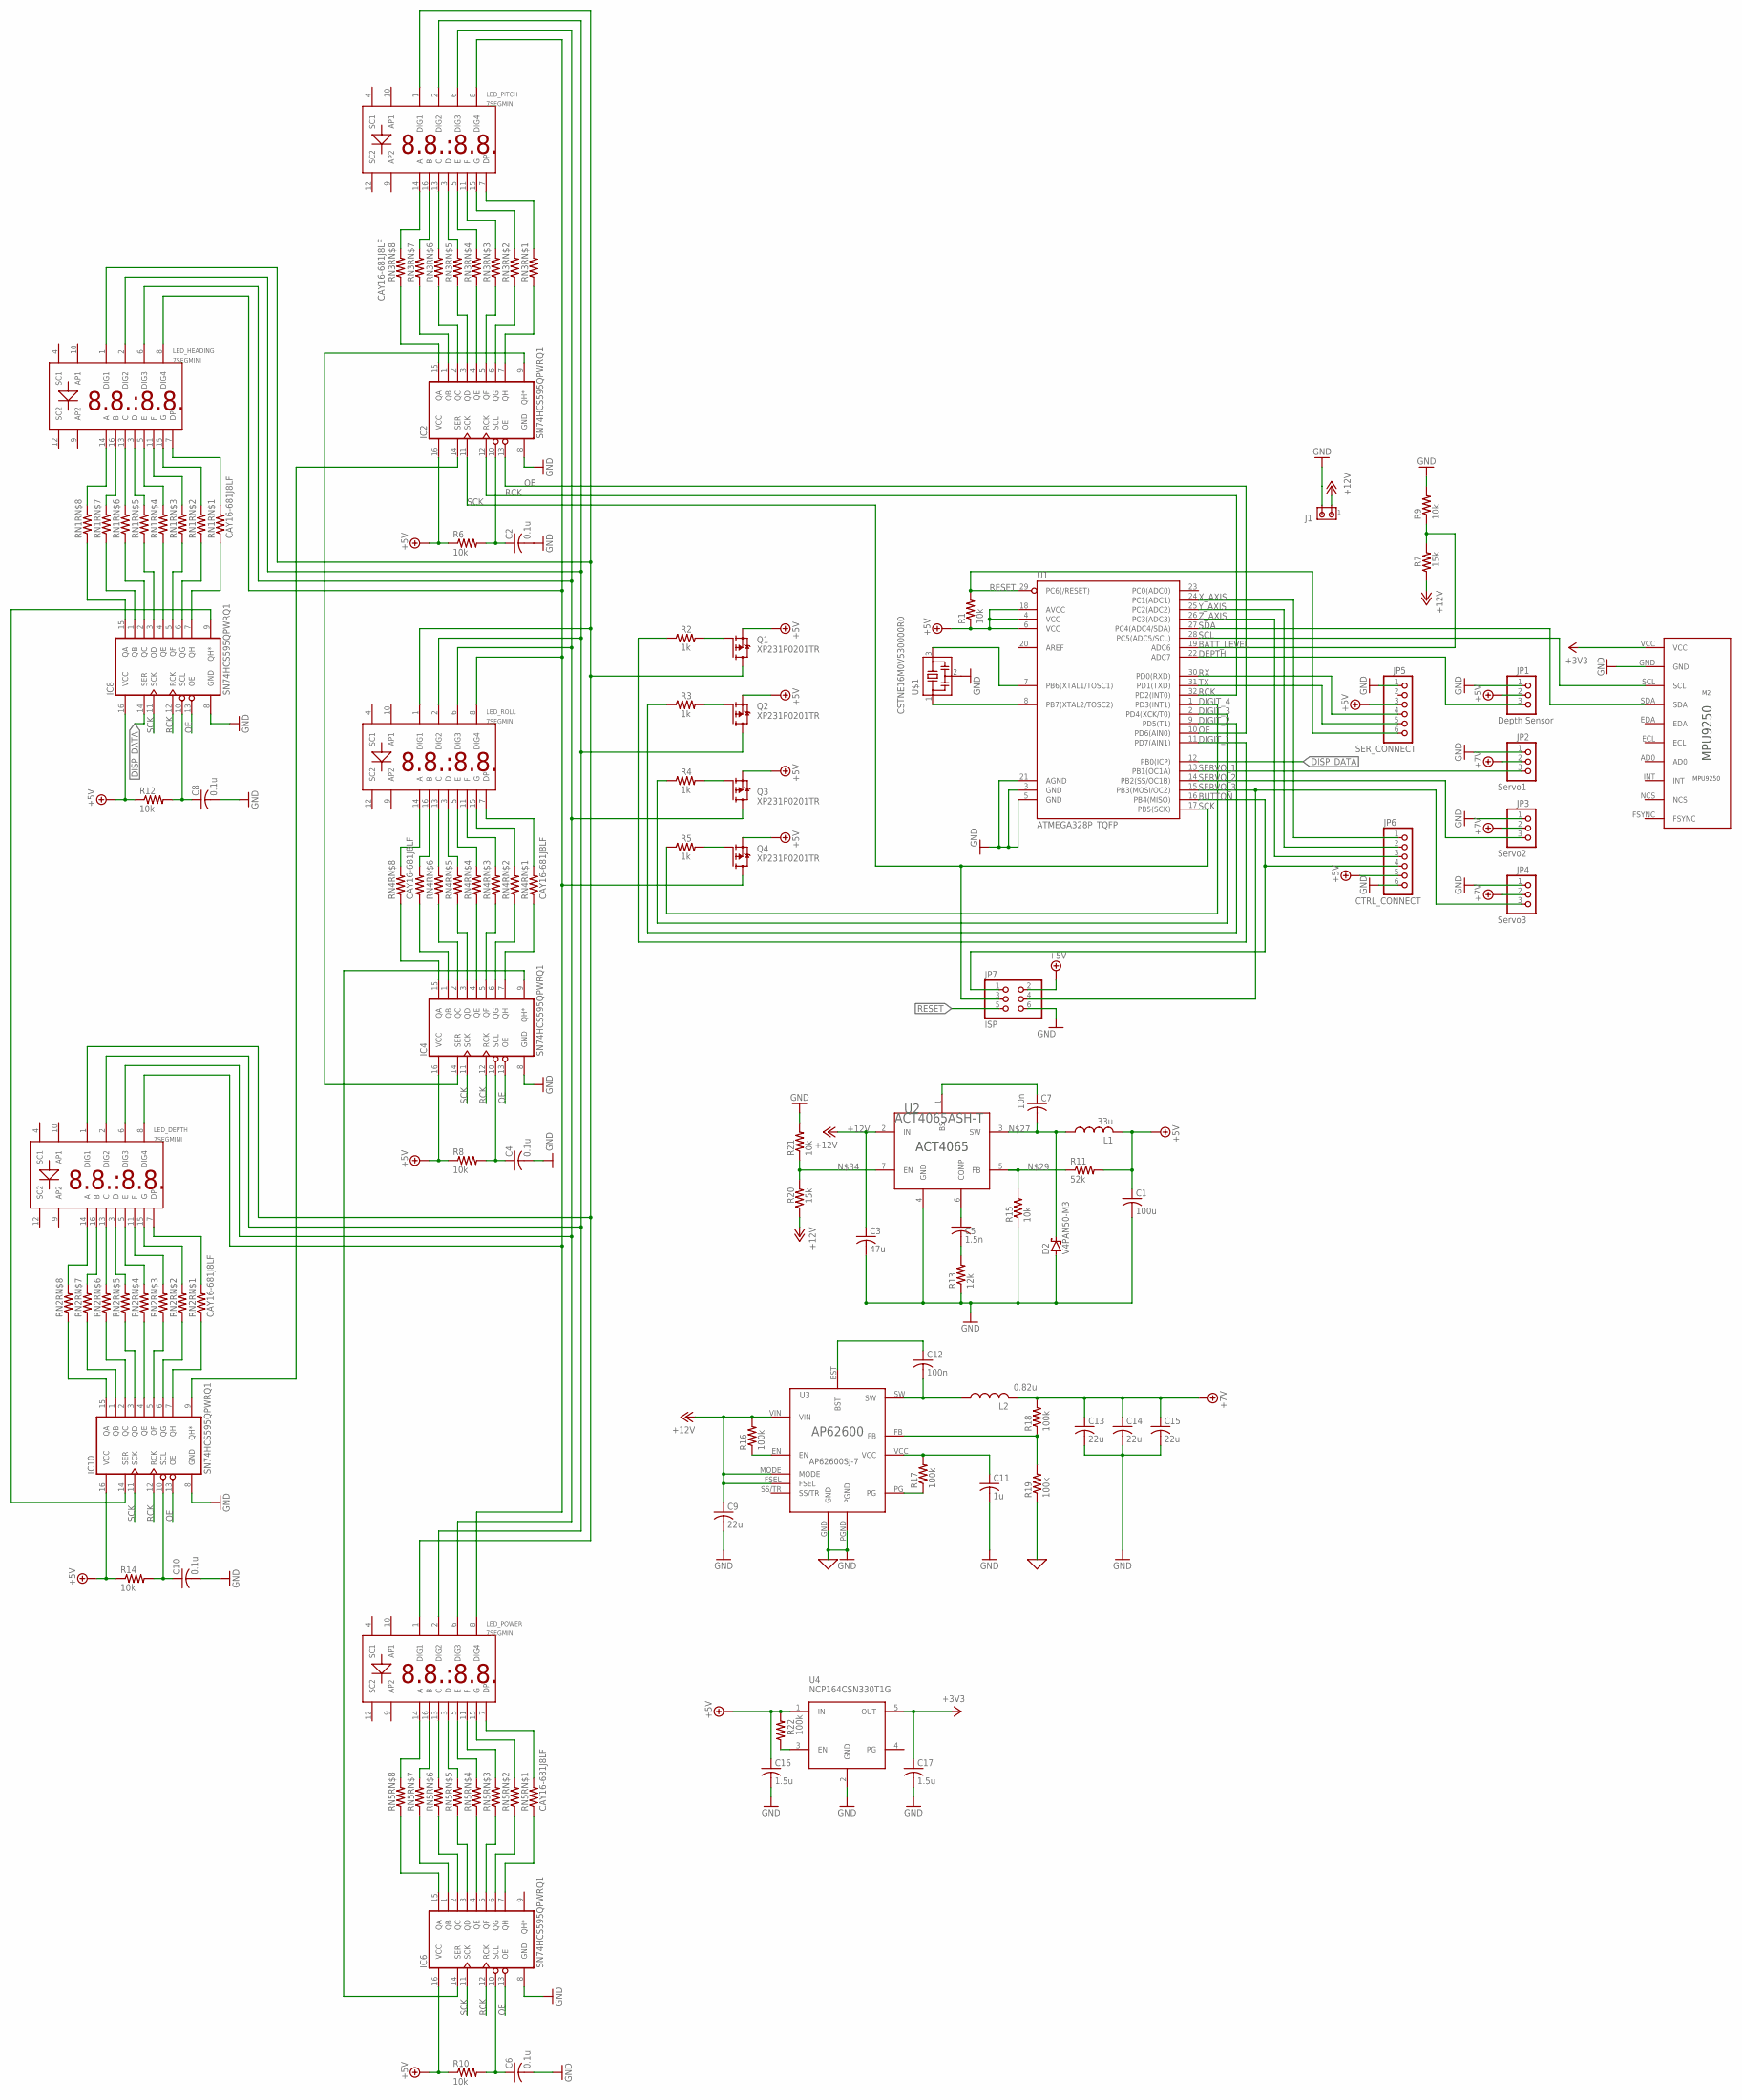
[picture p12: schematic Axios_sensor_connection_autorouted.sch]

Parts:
C1: 100u; C0603
C2, C4, C6, C8, C10: 0.1u; C0603
C3: 47u; C0603
C5: 1.5n; C0603
C7: 10n; C0603
C9, C13, C14, C15: 22u; C0603
C11: 1u; C0603
C12: 100n; C0603
C16, C17: 1.5u; C0603
D2: V4PAN50-M3; SMPA
IC2, IC4, IC6, IC8, IC10: SN74HCS595QPWRQ1; TSSOP16
J1: MTA02-156; 1X2MTA
JP1: Depth Sensor; 1X03
JP2: Servo1; 1X03
JP3: Servo2; 1X03
JP4: Servo3; 1X03
JP5: SER_CONNECT; 1X06
JP6: CTRL_CONNECT; 1X06
JP7: ISP; 2X03
L1: 33u; SRN1060-330M
L2: 0.82u; ECS-MPIL0630-R82MC
LED_DEPTH: 7SEGMINI
LED_HEADING: 7SEGMINI
LED_PITCH: 7SEGMINI
LED_POWER: 7SEGMINI
LED_ROLL: 7SEGMINI
M2: MPU9250
Q1, Q2, Q3, Q4: XP231P0201TR; SOT23
R1, R6, R8, R9, R10, R12, R14, R15, R21: 10k; R0603
R2, R3, R4, R5: 1k; R0603
R7, R20: 15k; R0603
R11: 52k; R0603
R13: 12k; R0603
R16, R17, R18, R19, R22: 100k; R0603
RN1, RN2, RN3, RN4, RN5: CAY16-681J8LF
U1: ATMEGA328P_TQFP; TQFP32-08
U2: ACT4065ASH-T; SO8
U3: AP62600SJ-7; V-QFN2030-12
U4: NCP164CSN330T1G; TSOP-5
U$1: CSTNE16M0V530000R0; CSTCR6M

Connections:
0: R19.1, U3.GND, U3.PGND
+3V3: C17.1, M2.VCC, U4.5 (OUT)
+5V: C1.1, C16.1, IC2.16 (VCC), IC4.16 (VCC), IC6.16 (VCC), IC8.16 (VCC), IC10.16 (VCC), JP1.2, JP2.2, JP3.2, JP4.2, JP5.3, JP6.5, JP7.2, L1.P$2 (2), Q1.2 (S), Q2.2 (S), Q3.2 (S), Q4.2 (S), R6.1, R8.1, R10.1, R11.2, R12.1, R14.1, R22.2, U4.1 (IN)
+7V: C13.1, C14.1, C15.1, L2.P$2 (2), R18.2
+12V: C3.1, C9.1, J1.1, R7.1, R16.2, R20.1, U2.2 (IN), U3.FSEL, U3.MODE, U3.VIN
BATT_LEVEL: R7.2, R9.1, U1.19 (ADC6)
BUTTON: JP6.4, JP7.1, U1.16 (PB4(MISO))
DEPTH: JP1.3, U1.22 (ADC7)
DIGIT_1: R2.1, U1.11 (PD7(AIN1))
DIGIT_2: R3.1, U1.9 (PD5(T1))
DIGIT_3: R4.1, U1.2 (PD4(XCK/T0))
DIGIT_4: R5.1, U1.1 (PD3(INT1))
DISP_DATA: IC8.14 (SER), U1.12 (PB0(ICP))
GND: C1.2, C2.2, C3.2, C4.2, C6.2, C8.2, C9.2, C10.2, C11.2, C13.2, C14.2, C15.2, C16.2, C17.2, D2.A, IC2.8 (GND), IC4.8 (GND), IC6.8 (GND), IC8.8 (GND), IC10.8 (GND), JP1.1, JP2.1, JP3.1, JP4.1, JP5.1, JP6.6, JP7.6, M2.GND, R9.2, R13.1, R15.1, R21.2, U1.3 (GND), U1.5 (GND), U1.21 (AGND), U2.4 (GND), U4.2 (GND), U$1.2
GND1: R17.1, U3.PG
GND2: R16.1, U3.EN
unnamed: R1.1, U1.4 (VCC), U1.6 (VCC), U1.18 (AVCC)
unnamed: IC8.9 (QH*), IC10.14 (SER)
unnamed: U1.8 (PB7(XTAL2/TOSC2)), U$1.1
unnamed: U1.7 (PB6(XTAL1/TOSC1)), U$1.3
unnamed: C7.1, U2.1 (BS)
unnamed: Q1.1 (G), R2.2
unnamed: Q2.1 (G), R3.2
unnamed: Q3.1 (G), R4.2
unnamed: Q4.1 (G), R5.2
unnamed: C7.2, D2.C, L1.P$1 (1), U2.3 (SW)
unnamed: R11.1, R15.2, U2.5 (FB)
unnamed: R22.1, U4.3 (EN)
unnamed: C5.2, R13.2
unnamed: R20.2, R21.1, U2.7 (EN)
unnamed: C5.1, U2.6 (COMP)
unnamed: C11.1, R17.2, U3.VCC
unnamed: C12.2, L2.P$1 (1), U3.SW
unnamed: R18.1, R19.2, U3.FB
unnamed: LED_PITCH.14 (A), RN3.9 (2)
unnamed: LED_PITCH.16 (B), RN3.10 (2)
unnamed: LED_PITCH.13 (C), RN3.11 (2)
unnamed: LED_PITCH.3 (D), RN3.12 (2)
unnamed: LED_PITCH.5 (E), RN3.13 (2)
unnamed: LED_PITCH.11 (F), RN3.14 (2)
unnamed: LED_PITCH.15 (G), RN3.15 (2)
unnamed: LED_PITCH.7 (DP), RN3.16 (2)
unnamed: IC2.15 (QA), RN3.8 (1)
unnamed: IC2.1 (QB), RN3.7 (1)
unnamed: IC2.2 (QC), RN3.6 (1)
unnamed: IC2.3 (QD), RN3.5 (1)
unnamed: IC2.4 (QE), RN3.4 (1)
unnamed: IC2.5 (QF), RN3.3 (1)
unnamed: IC2.6 (QG), RN3.2 (1)
unnamed: IC2.7 (QH), RN3.1
unnamed: C2.1, IC2.10 (SCL), R6.2
unnamed: C12.1, U3.BST
unnamed: IC2.14 (SER), IC10.9 (QH*)
unnamed: LED_ROLL.14 (A), RN4.9 (2)
unnamed: LED_ROLL.16 (B), RN4.10 (2)
unnamed: LED_ROLL.13 (C), RN4.11 (2)
unnamed: LED_ROLL.3 (D), RN4.12 (2)
unnamed: LED_ROLL.5 (E), RN4.13 (2)
unnamed: LED_ROLL.11 (F), RN4.14 (2)
unnamed: LED_ROLL.15 (G), RN4.15 (2)
unnamed: LED_ROLL.7 (DP), RN4.16 (2)
unnamed: IC4.15 (QA), RN4.8 (1)
unnamed: IC4.1 (QB), RN4.7 (1)
unnamed: IC4.2 (QC), RN4.6 (1)
unnamed: IC4.3 (QD), RN4.5 (1)
unnamed: IC4.4 (QE), RN4.4 (1)
unnamed: IC4.5 (QF), RN4.3 (1)
unnamed: IC4.6 (QG), RN4.2 (1)
unnamed: IC4.7 (QH), RN4.1
unnamed: C4.1, IC4.10 (SCL), R8.2
unnamed: IC2.9 (QH*), IC4.14 (SER)
unnamed: LED_POWER.14 (A), RN5.9 (2)
unnamed: LED_POWER.16 (B), RN5.10 (2)
unnamed: LED_POWER.13 (C), RN5.11 (2)
unnamed: LED_POWER.3 (D), RN5.12 (2)
unnamed: LED_POWER.5 (E), RN5.13 (2)
unnamed: LED_POWER.11 (F), RN5.14 (2)
unnamed: LED_POWER.15 (G), RN5.15 (2)
unnamed: LED_POWER.7 (DP), RN5.16 (2)
unnamed: IC6.15 (QA), RN5.8 (1)
unnamed: IC6.1 (QB), RN5.7 (1)
unnamed: IC6.2 (QC), RN5.6 (1)
unnamed: IC6.3 (QD), RN5.5 (1)
unnamed: IC6.4 (QE), RN5.4 (1)
unnamed: IC6.5 (QF), RN5.3 (1)
unnamed: IC6.6 (QG), RN5.2 (1)
unnamed: IC6.7 (QH), RN5.1
unnamed: C6.1, IC6.10 (SCL), R10.2
unnamed: IC4.9 (QH*), IC6.14 (SER)
unnamed: LED_HEADING.14 (A), RN1.9 (2)
unnamed: LED_HEADING.16 (B), RN1.10 (2)
unnamed: LED_HEADING.13 (C), RN1.11 (2)
unnamed: LED_HEADING.3 (D), RN1.12 (2)
unnamed: LED_HEADING.5 (E), RN1.13 (2)
unnamed: LED_HEADING.11 (F), RN1.14 (2)
unnamed: LED_HEADING.15 (G), RN1.15 (2)
unnamed: LED_HEADING.7 (DP), RN1.16 (2)
unnamed: IC8.15 (QA), RN1.8 (1)
unnamed: IC8.1 (QB), RN1.7 (1)
unnamed: IC8.2 (QC), RN1.6 (1)
unnamed: IC8.3 (QD), RN1.5 (1)
unnamed: IC8.4 (QE), RN1.4 (1)
unnamed: IC8.5 (QF), RN1.3 (1)
unnamed: IC8.6 (QG), RN1.2 (1)
unnamed: IC8.7 (QH), RN1.1
unnamed: C8.1, IC8.10 (SCL), R12.2
unnamed: LED_DEPTH.1 (DIG1), LED_HEADING.1 (DIG1), LED_PITCH.1 (DIG1), LED_POWER.1 (DIG1), LED_ROLL.1 (DIG1), Q1.3 (D)
unnamed: LED_DEPTH.2 (DIG2), LED_HEADING.2 (DIG2), LED_PITCH.2 (DIG2), LED_POWER.2 (DIG2), LED_ROLL.2 (DIG2), Q2.3 (D)
unnamed: LED_DEPTH.6 (DIG3), LED_HEADING.6 (DIG3), LED_PITCH.6 (DIG3), LED_POWER.6 (DIG3), LED_ROLL.6 (DIG3), Q3.3 (D)
unnamed: LED_DEPTH.8 (DIG4), LED_HEADING.8 (DIG4), LED_PITCH.8 (DIG4), LED_POWER.8 (DIG4), LED_ROLL.8 (DIG4), Q4.3 (D)
unnamed: LED_DEPTH.14 (A), RN2.9 (2)
unnamed: LED_DEPTH.16 (B), RN2.10 (2)
unnamed: LED_DEPTH.13 (C), RN2.11 (2)
unnamed: LED_DEPTH.3 (D), RN2.12 (2)
unnamed: LED_DEPTH.5 (E), RN2.13 (2)
unnamed: LED_DEPTH.11 (F), RN2.14 (2)
unnamed: LED_DEPTH.15 (G), RN2.15 (2)
unnamed: LED_DEPTH.7 (DP), RN2.16 (2)
unnamed: IC10.15 (QA), RN2.8 (1)
unnamed: IC10.1 (QB), RN2.7 (1)
unnamed: IC10.2 (QC), RN2.6 (1)
unnamed: IC10.3 (QD), RN2.5 (1)
unnamed: IC10.4 (QE), RN2.4 (1)
unnamed: IC10.5 (QF), RN2.3 (1)
unnamed: IC10.6 (QG), RN2.2 (1)
unnamed: IC10.7 (QH), RN2.1
unnamed: C10.1, IC10.10 (SCL), R14.2
OE: IC2.13 (OE), IC4.13 (OE), IC6.13 (OE), IC8.13 (OE), IC10.13 (OE), U1.10 (PD6(AIN0))
RCK: IC2.12 (RCK), IC4.12 (RCK), IC6.12 (RCK), IC8.12 (RCK), IC10.12 (RCK), U1.32 (PD2(INT0))
RESET: JP5.6, JP7.5, R1.2, U1.29 (PC6(/RESET))
RX: JP5.4, U1.30 (PD0(RXD))
SCK: IC2.11 (SCK), IC4.11 (SCK), IC6.11 (SCK), IC8.11 (SCK), IC10.11 (SCK), JP7.3, U1.17 (PB5(SCK))
SCL: M2.SCL, U1.28 (PC5(ADC5/SCL))
SDA: M2.SDA, U1.27 (PC4(ADC4/SDA))
SERVO_1: JP2.3, U1.13 (PB1(OC1A))
SERVO_2: JP3.3, U1.14 (PB2(SS/OC1B))
SERVO_3: JP4.3, JP7.4, U1.15 (PB3(MOSI/OC2))
TX: JP5.5, U1.31 (PD1(TXD))
X_AXIS: JP6.1, U1.24 (PC1(ADC1))
Y_AXIS: JP6.2, U1.25 (PC2(ADC2))
Z_AXIS: JP6.3, U1.26 (PC3(ADC3))

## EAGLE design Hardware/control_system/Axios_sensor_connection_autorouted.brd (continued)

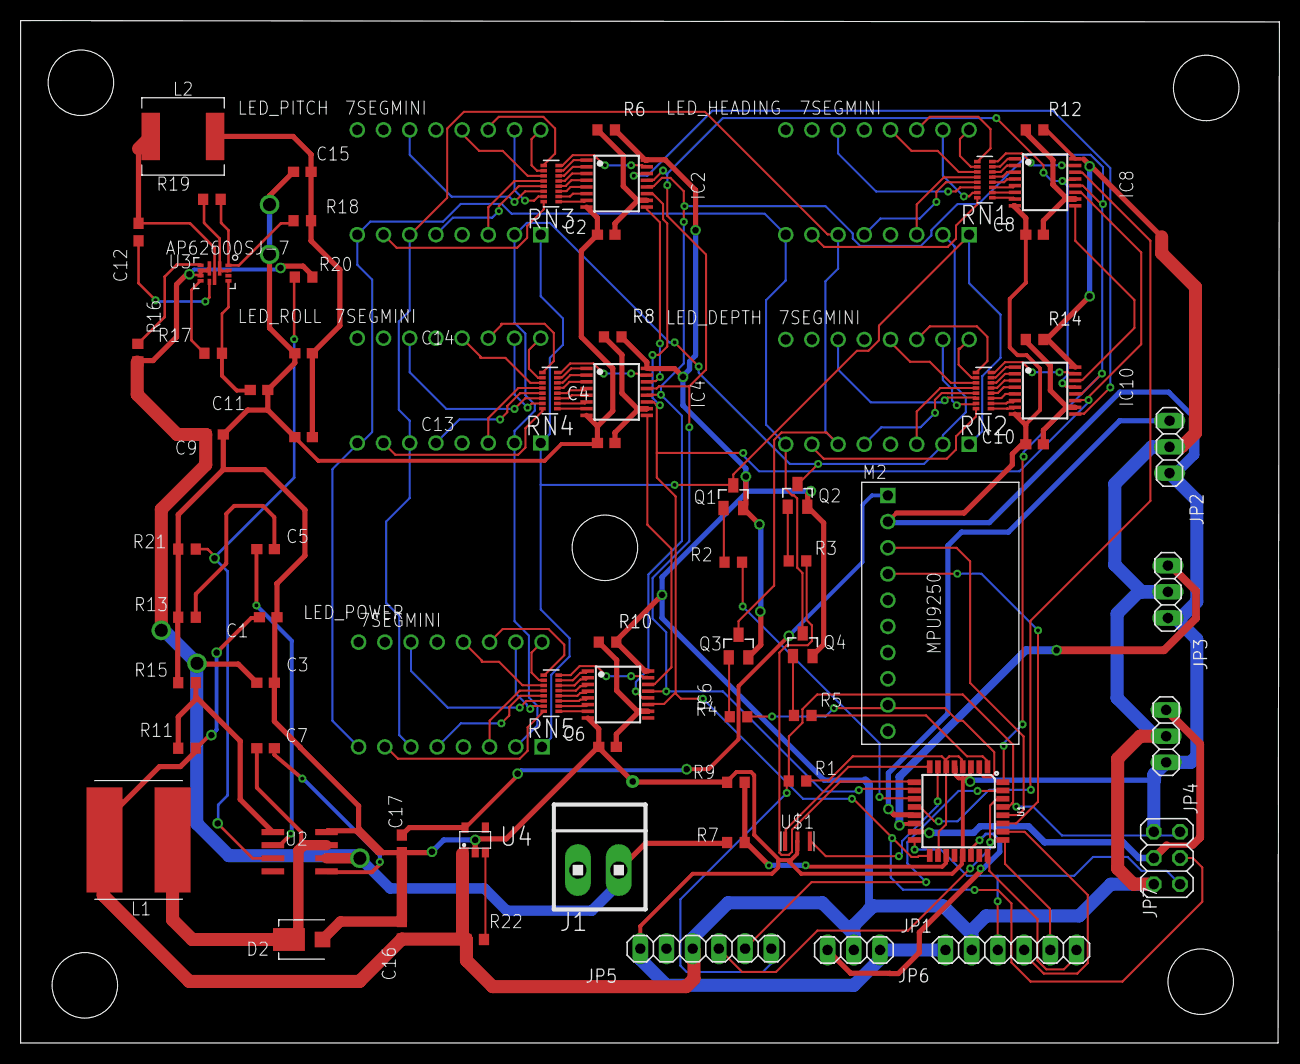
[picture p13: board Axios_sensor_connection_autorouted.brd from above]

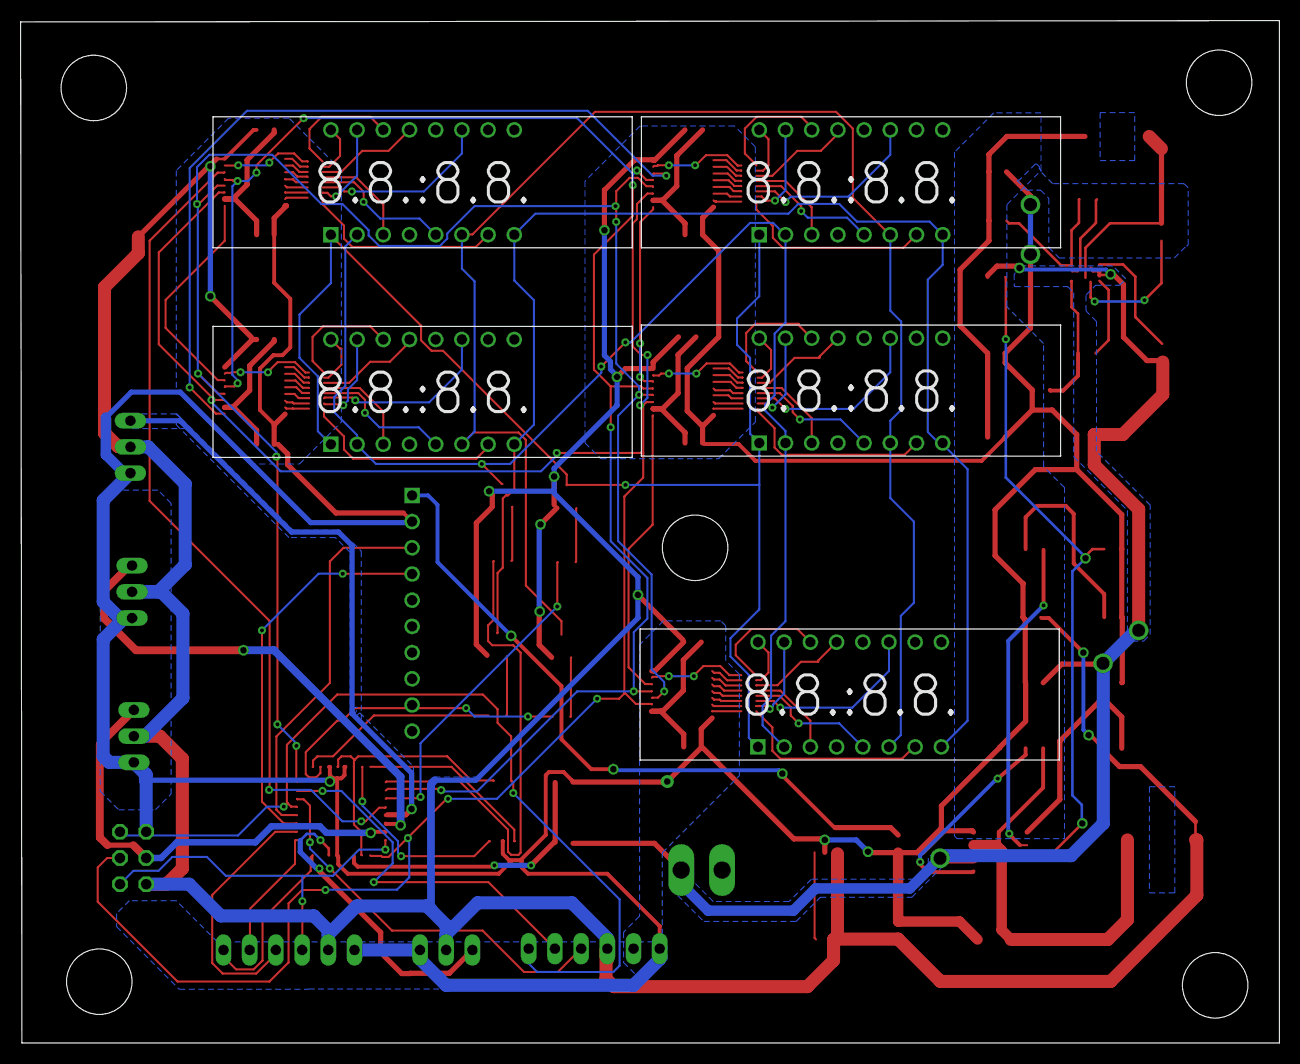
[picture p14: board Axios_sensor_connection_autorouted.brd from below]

Board: 2 copper layers, 122.0 x 99.1 mm, 75 parts (5 on the bottom side), 141 nets.

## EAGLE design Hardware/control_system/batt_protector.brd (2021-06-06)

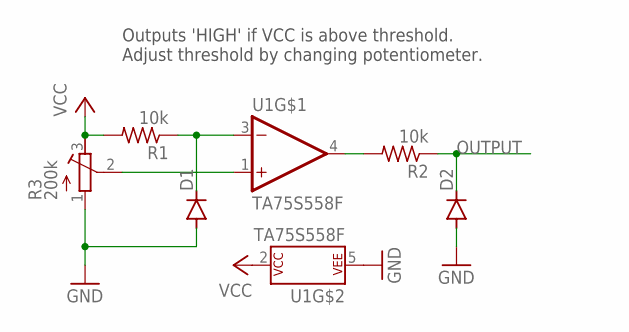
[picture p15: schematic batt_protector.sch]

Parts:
D1, D2: DIODE-SOD323-R; SOD323-R
R1, R2: 10k; R0603
R3: 200k; RTRIM64P
U1: TA75S558F; SOTFL95P275X130-5N

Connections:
GND: D1.A, D2.A, R3.1 (A), U1.5 (P$V-)
INPUT: R3.2 (S), U1.1 (+IN)
unnamed: R2.2, U1.4 (OUT)
OUTPUT: D2.C, R2.1
REFV: D1.C, R1.1, U1.3 (-IN)
VCC: R1.2, R3.3 (E), U1.2 (P$V+)

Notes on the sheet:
Outputs 'HIGH' if VCC is above threshold. Adjust threshold by changing potentiometer.

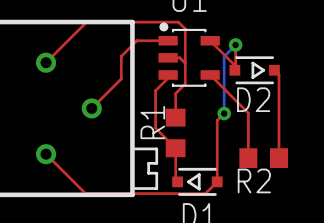
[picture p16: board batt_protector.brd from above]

Board: 2 copper layers, 6 parts (0 on the bottom side), 6 nets.

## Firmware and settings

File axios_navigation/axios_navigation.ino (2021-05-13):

//#define DEBUGMODE

#include <Servo.h>

#include "display.h"
#include "pin_assignments.h"
#include "fin.h"
#include "mpu.h"

const unsigned long atmosphericPressure = 102400UL; // Pa
const unsigned long depthDivisor = 9807UL; // "Weight density" of water (kg/m^3) * g (m/s^2)

Servo finServo[3]; // Ordered top, left, right

const int displayRefreshPeriod = 100; // Period between updates ms
unsigned long displayUpdateMark;

int powerReading; // Power reading from pedals

void setup() {
  Serial.begin(9600); // Used for debugging or power communication

#ifdef DEBUGMODE
  Serial.println(F("AXIOS CONTROL SYSTEM\n"));
  delay(100);
#endif

  // Displays
  displaySetup();

#ifdef DEBUGMODE
  Serial.println(F("Displays configured."));
#endif

  // MPU
  mpuSetup();

  // Calibrate IMU if requested
  if (digitalRead(leftPressedPin) == false) {
#ifdef DEBUGMODE
    Serial.println(F("Calibrating MPU9250 by user request."));
#endif
    
    mpuCalibrate();
  }

  for (byte i = 0; i < 3; i++) {
    finServo[i].attach(servoPins[i]);
  }
}


void loop() {
  mpu.update(); // Update MPU readings
  steerSub();

  // Read in power as a byte (byte value is half the real value)
  if (Serial.available()) {
    powerReading = 2 * Serial.read();
  }

  // Update screens periodically
  if (millis() > displayUpdateMark) {

    // Displays in order: POWER (0), ROLL, PITCH, DEPTH, HEADING (4)
    // Note: Due to the relative heading of the IMU to the board
    // Pitch and roll are swapped, heading is made negative

    displayFloat(mpu.getPitch(), 2, 0); // Roll display
    displayFloat(mpu.getRoll(), 1, 0); // Pitch display
    displayFloat(mpu.getYaw(), 0, 0); // Yaw is equal to heading

    //displayFloat(getDepth(), 3, 2);
    //displayInt(powerReading, 4);

    displayUpdateMark = millis() + displayRefreshPeriod;

#ifdef DEBUGMODE
    mpu.printRollPitchYaw();
#endif
  }

#ifdef DEBUGMODE
  Serial.println();
  delay(1000);
#endif
}

void steerSub() {
  // Get the input along each axis from -1 to +1 at each extreme

  float inputs[] = {rightHorizontalPin, rightVerticalPin, leftHorizontalPin};

  for (byte i = 0; i < 3; i++) {
    inputs[i] = analogRead(inputs[i]);

    inputs[i] = float(inputs[i] - axisCenters[i]);

    if (abs(inputs[i]) < deadzone) inputs[i] = 0;
    else {
      if (inputs[i] < 0) {
        inputs[i] = inputs[i] / float(axisCenters[i]);
      }
      else {
        inputs[i] = inputs[i] / float(1024 - axisCenters[i]);
      }
    }
  }

  // Assign each input to a different axis
  float directions[3]; // Stores direction values. Pitch, roll, yaw.
  directions[0] = inputs[0]; // Pitch
  directions[1] = inputs[2]; // Roll
  directions[2] = inputs[1]; // Yaw

  float finAngles[] = {0, 0, 0};
  float scaling = vectorScaling; // How much the vector is scaled
  // Needs to be a variable starting at default value to be tweaked if needed

  for (byte servo = 0; servo < 3; servo++) {

    // Use inverse matrix to get needed fin angles
    for (byte axis = 0; axis < 3; axis++) {
      finAngles[servo] = finAngles[servo] + (directions[axis] * invert[servo][axis]);
    }


    // See if scaled angle would exceed limits
    // If it does find the factor to scale it to the limit
    if ((finAngles[servo] * scaling) > maxFinAngle) {
#ifdef DEBUGMODE
      Serial.println(F("UPPER LIMIT"));
      Serial.println(finAngles[servo]* scaling);
#endif

      scaling = maxFinAngle / finAngles[servo];
#ifdef DEBUGMODE
      Serial.println(scaling);
#endif
    }
    else if ((finAngles[servo] * scaling) < minFinAngle) {
#ifdef DEBUGMODE
      Serial.println(F("LOWER LIMIT"));
      Serial.println(finAngles[servo]* scaling);
#endif

      scaling = minFinAngle / finAngles[servo];
#ifdef DEBUGMODE
      Serial.println(scaling);
#endif
    }

  }
#ifdef DEBUGMODE
  Serial.println(F("RESULTING ANGLES"));
#endif
  // Scale angles (so none exceed limits) and write to servos
  for (byte servo = 0; servo < 3; servo++) {
    finAngles[servo] = finAngles[servo] * scaling;
#ifdef DEBUGMODE
    Serial.print(finAngles[servo]);
    Serial.print(F(" - "));
    Serial.println(servoAngFin(finAngles[servo]));
#endif

    finServo[servo].write(servoAngFin(finAngles[servo]));
  }
}



int servoAngFin(float finAngle) {
  // Convert fin angle to servo using a LUT
  // LUT index is increments of 0.5deg from min (0) to max fin angles

  byte index = byte(round(finAngle * 2));

  index = constrain(index, 2 * minFinAngle, 2 * maxFinAngle);
  // Make sure it's in the working range

  index = index - (2 * minFinAngle);

  return angleLUT[index];
}

float getDepth() {
  float depth = 0;

  /* Derived forumla for depth using our sensor

     (10 * analogRead - 1024) * 9375 - 64 * Patm (in Pa)
     ----------------------------------------------------
             64 * g * density of water (kg/m^3)
  */
  unsigned long temp;

  temp = 10 * analogRead(depthPin);
  temp = temp - 1024;
  temp = temp * 9375UL; // Pressure * 64

  temp = temp - (64 * atmosphericPressure);

  depth = float(temp) / float(64 * depthDivisor);
  return depth;
}

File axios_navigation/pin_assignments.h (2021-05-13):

#ifndef PIN_HEADER
#define PIN_HEADER
/* Pin Allocations

    Control Related:
    A1 - "X" axis - Right Horizontal
    A2 - "Y" axis - Right Vertical
    A3 - "Z" axis - Left Horizontal
    D12 - PB4 - Left pressed

    D9 - PB1 - Servo 1
    D10 - PB2 - Servo 2
    D11 - PB3 - Servo 3

    Sensing:
    A6 - Battery Level
    A7 - Depth

    Display Pins:
    PD3 - Digit 4
    PD4 - Digit 3
    PD5 - Digit 2
    PD7 - Digit 1

    PD2 - Output clock
    PD6 - Output enable
    PB0 - Display data
    PB5 - Display clock
    
    Displays in order: POWER (0), ROLL, PITCH, DEPTH, HEADING (4)
*/

const byte leftHorizontalPin = A3;
const byte rightHorizontalPin = A1;
const byte rightVerticalPin = A2;
const byte leftPressedPin = 12;

const byte servoPins[] = {9,10, 11}; // Servos: top, left, right

const byte batteryPin = A6;
const byte depthPin = A7;

#endif

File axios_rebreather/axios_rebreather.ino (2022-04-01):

/* Pin Allocations

    Port C (Analog, referred to as "A_"):
    2 - Calibration 3
    3 - Calibration 2
    4 - Calibration 1
    5 - Oxygen 3
    6 - Oxygen 2
    7 - Oxygen 1

    Port D (Digital, D0 to D7)
    2 - D2 - CO2 Sensor (Inverted input)
    3 - D3 - Output enable for displays (brightness)
    4 - D4 - Shift Register Data
    5 - D5 - Data clock
    6 - D6 - Output clock
    7 - D7 - Digit 1

    Port B (Digits, D8 and up)
    0 - D8 - Digit 2
    1 - D9 - Digit 3
    2 - D10 - Digit 4
*/

#include "display.h"

// Oxygen related pins
const byte oxygenSensor[] = {A7, A6, A5};
const byte oxygenCalibration[] = {A4, A3, A2};


// CO2 related pin and variables
const byte CO2Sensor = 2; // CO2 sensor pin
const int CO2Span = 5000;                     // Span in ppm of CO2 of sensor
const long CO2WarmUp = 180000;                // CO2 sensor warmup time in ms (datasheet says 3 minutes)
volatile unsigned long CO2Level = 400;        // 400ish is ambient so good default
volatile unsigned long lastRising, lastFalling;

// Screen numbers
const byte CO2Screen = 0;
const byte O2Screen[] = {3, 2, 1};

#define TESTMODE // Uncomment for just showing random/test data on displays

void setup() {

  displaySetup();

  // Set up CO2 sensor routine to run on PWM changes
  pinMode(CO2Sensor, INPUT_PULLUP);
  attachInterrupt(digitalPinToInterrupt(CO2Sensor), CO2Interrupt, CHANGE);

  //Serial.begin(9600);
}


void loop() {

#ifdef TESTMODE
  // Show random numbers on the middle two displays
  //displayInt(random(10000), O2Screen[random(2) + 1]);
  //displayFloat(millis() / 1000.0, O2Screen[0], 1);  // Time running on top display

  // Work through readings of a particular sensor (useful for initial calibrations)
  const byte oxygenSensorOfInterest = 2; 
  
  noInterrupts();
  delayMicroseconds(10); // A bit for noise to dissappear
  displayInt(analogRead(oxygenSensor[oxygenSensorOfInterest]), O2Screen[0]);
  displayInt(analogRead(oxygenCalibration[oxygenSensorOfInterest]), O2Screen[1]);
  displayFloat(oxygenRead(2), O2Screen[oxygenSensorOfInterest], 2);
  interrupts();
    
  displayInt(digitalRead(CO2Sensor), CO2Screen);  // Show state of sensor
#else

  // Read oxygen levels, display them appropriately (dashes if over 100%)
  for (byte i = 0; i < 3; i++) {
    if (oxygenRead(i) < 100.0) displayFloat(oxygenRead(i), O2Screen[i], 2);
    else displayDashes(O2Screen[i]);
  }

  
  // CO2, shows value or countdown to when the sensor's ready if too early

  if (millis() < CO2WarmUp) displayFloat((CO2WarmUp - millis()) / 1000.0, CO2Screen, 1); // Warmup countdown (decimal indicates not CO2)
  else displayInt(CO2Level, CO2Screen);               // Sensor should be operational
#endif

  delay(100);
}

void CO2Interrupt () {
  // Based on time high and low for a PWM cycle, in milliseconds (total period ~1004ms)

  // NOTE THE PWM IS INVERTED BY THE LEVEL SHIFTER, HENCE THE SEEMINGLY CONTRADICTORY PIN STATES

  unsigned long currentTime = millis();

  if (digitalRead(CO2Sensor) == HIGH) {
    lastFalling = currentTime; // Mark falling edge of PWM
  }
  else {
    // Rising edge, start of a new pulse

    // Calculate CO2 level from last pulse
    // CO2 = ppm span * (Th - 2ms) / (Th + Tl - 4ms)

    unsigned long timeHigh = lastFalling - lastRising;
    unsigned long timeLow = currentTime - lastFalling;

    CO2Level = CO2Span * (timeHigh - 2);
    CO2Level = CO2Level / (timeHigh + timeLow - 4);

    lastRising = currentTime; // Update rising time
  }
}

float oxygenRead(byte sensor) {
  // Oxygen value calculations

  
  // Get analog values
  // Need to disable interrupts so display code doesn't cause noise when reading
  noInterrupts();
  delayMicroseconds(10); // A bit for noise to dissappear

  // Using int since it is faster
  int OR = analogRead(oxygenSensor[sensor]);          // Oxygen sensor reading
  int cal = analogRead(oxygenCalibration[sensor]);    // This is the calibration value.

  interrupts();

  // Math
  float b = float(cal) / 21.0;
  float m = (1010.0 - float(cal)) / 79.0; // This is the gradient (slope) of the function.
  float oxy = (float(OR) - b) / m;     // This is the oxygen value.

  return (oxy);
}

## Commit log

2021-05-13 Initial commit of current code
    Rebreather code is basically done. Navigation code needs some work especially with the orientation data.
2021-06-06 Uploaded hardware related files
    The boards were designed using EAGLE
    [Axios_sensor_connection_autorouted.brd, Axios_sensor_connection_autorouted.sch, Oxygen Sensor & CO2 PWM.brd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]
2022-04-01 Fixing CO2 sensor span
    CO2 sensor was labelled with a span of 5000ppm, not 2000
    [axios_rebreather.ino]
2022-04-01 Modified oxygen reading code against noise
    Needed to make the system read uninterrupted since the displays getting updated produces significant noise.
    [axios_rebreather.ino]

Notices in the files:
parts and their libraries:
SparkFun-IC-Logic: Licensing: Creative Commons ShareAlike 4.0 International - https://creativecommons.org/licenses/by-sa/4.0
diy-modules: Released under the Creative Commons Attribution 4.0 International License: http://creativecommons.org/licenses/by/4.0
